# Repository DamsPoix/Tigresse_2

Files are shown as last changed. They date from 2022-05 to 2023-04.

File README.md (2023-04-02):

# Tigresse_2

<p align="center">
  
</p>

Ce projet nommé Tigresse-2 est un projet de Fusée expérimentale qui volera lors de la campagne de lancement 2022 organisé par le Centre National d'Etudes Spatiales. Cette campagne, nommée C'Space regroupe tous les clubs spatiaux de France et de temps en temps des clubs spatiaux d'autres pays. 
Tigresse-2 est la seconde fusée expérimentale de l'association de l'air et de l'espace de l'université d'Orléans Space Tech Orléans.

Elle emportera une expérience afin de mesurer les résonnances de Schumann durant sa phase de redescente sous parachute.

<p align="center">
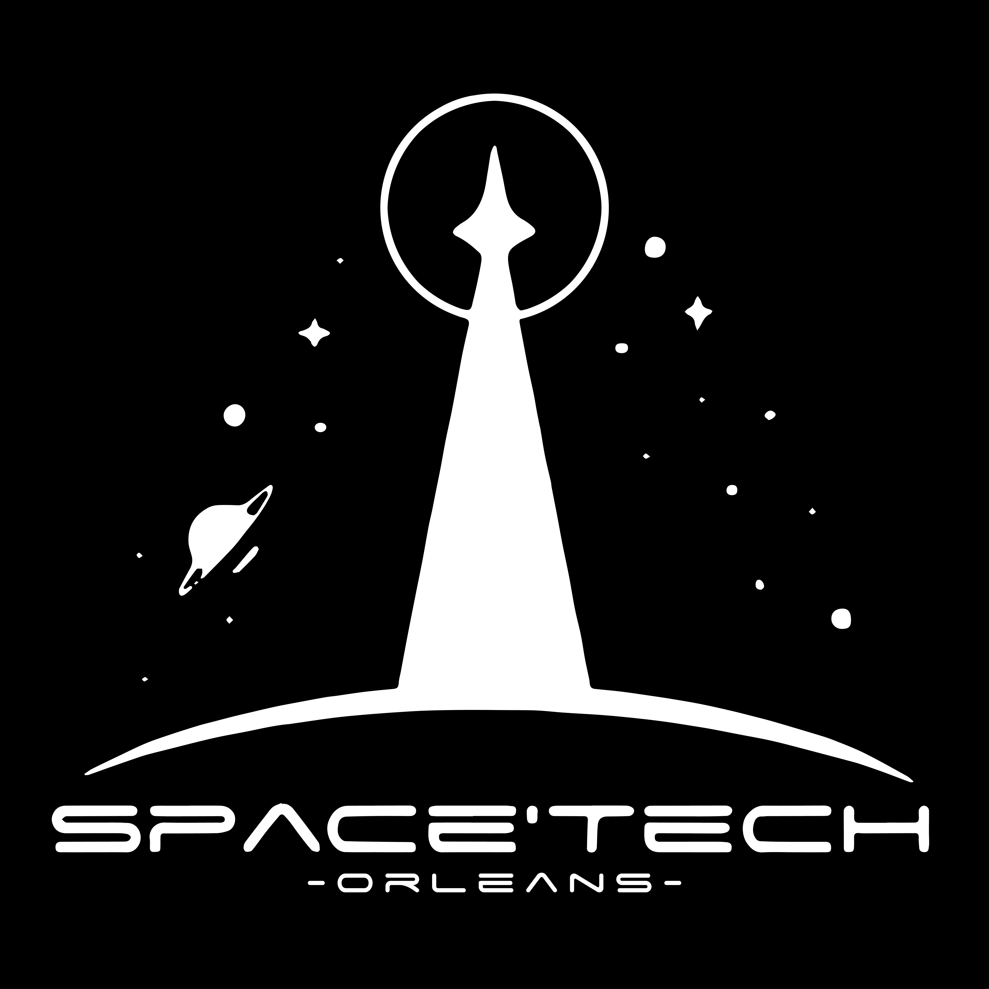
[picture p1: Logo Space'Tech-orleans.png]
  
</p>
La fusée a d'une hauteur de 1 mètre 85 avec une peau aluminium. L'ogive mesure 45cm.
<p align="center">
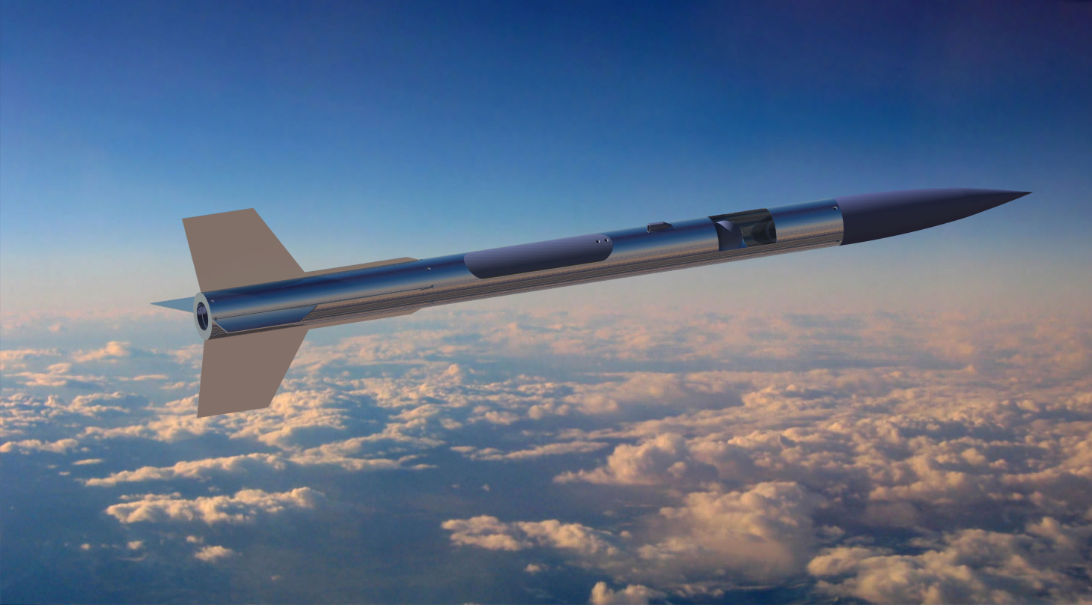
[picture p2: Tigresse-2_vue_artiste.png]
  
</p>
"""UPDATE"""

Après une campagne de lancements de fusées au C'Space 2022, Tigresse-2 a effectué un vol nominal ! 
Voici l'équipe qui a permit ce vol parfait : 

De gauche à droite : Aymerick BATS (responsable expérience) - Loup-Maël AGULES(support technique) - Raynald DUMAS (responsable vision fusée) - Léo MARMANDE (support technique) - Hugo KREMER (responsable mécanique) - Damien POIX (chef de projet/responsable seq et CAO) - Corentin LAROCHE (responsable télémétrie).
</p>
<p align="center">
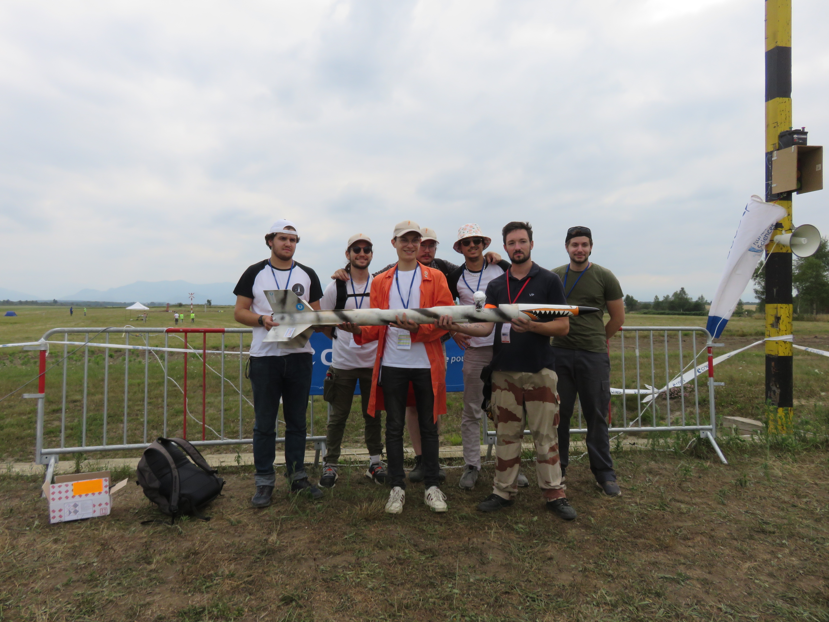
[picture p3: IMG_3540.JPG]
  
</p>

Lien vers GrabCad : <a href="https://grabcad.com/library/tigresse-2-1" target="_blank">Grabcad Tigresse-2</a>

Merci au CNES et à Planète Science pour cette opportunité ! 
Merci à l'équipe pour leur détermination et leur travail ! 

Go Space'Tech, Go Tigresse !

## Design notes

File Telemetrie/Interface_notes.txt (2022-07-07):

courbe avec la projection de trajectoire (+ data : altitude, acceleration, speed, timer)
carte avec la trajectoire vue de haut
attitude
stages (idle, liftoff, MECO, Apoapsis, Parachute deploy, landing)
logs (etats, erreurs, etat liaison GPS...)
control pannel :
	- enregistrer le raw data input (GQRX ou quoi, vraiment la Bande passante quoi)
	- exporter les données importante a sauvegarder au sol au cas ou (magnéto, GPS)
	- exporter la trajectoire pour récupération sur téléphone

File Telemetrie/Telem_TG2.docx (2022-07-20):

Télémétrie Tigresse

# Contexte

Dans le cadre du CSpace … t’as compris, la flemme. Avec un délais court de développement, de nombreux raccourcis ont été pris lors de la conception de ce système.

Cette documentation est clairement une ébauche.

# Besoins

La télémétrie doit permettre un suivi en temps réel et la récupération de la fusée après sa mission.

Elle sera constituée d’une charge utile et d’une station sol.

Un magnétomètre 3 axes devra être implémenté pour échantillonner les variations magnétiques pour l’expérience des résonnances de Schumann.

# Contraintes

Interdiction d’utiliser un récepteur télémétrique en zone pyrotechniques

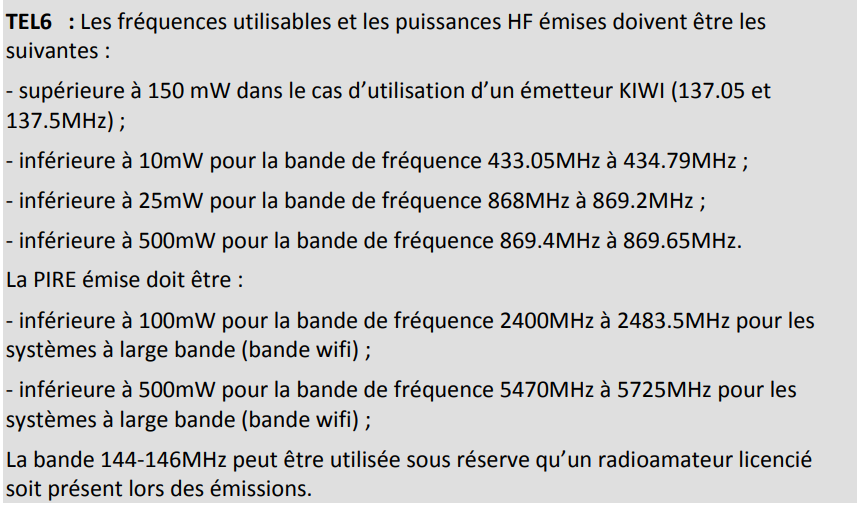
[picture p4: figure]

Alimentation indépendante, avec interrupteur de mise en marche indépendant.

Autonomie de 3h minimum.

Le Taux d’Onde Stationnaires (TOS) doit être inférieur à 2 pour la fréquence d’émission (avec connectique BNC).

Arrêtez l’émission 10 minutes après le lancement (Impératif)

# Problématiques

GPS : high rate / CoCom limit (< 18.000m & < 1000 knots)

Précision GPS

Perte de de signal GPS & Downlink

# Solutions proposées

## Charge utile :

La charge utile doit permettre l’envoie de donnée nécessaire au suivi et à la récupération de la fusée. Elle doit également permettre de valider et enregistrer les performances de celle-ci.

### Localisation :

Afin de permettre la localisation de la fusée dans l’espace, la CU devra embarquer un GPS, une centrale inertielle et un altimètre. Une fusion de ces 3 éléments doit permettre la localisation du lanceur à des fins de performances, et de tracking(si implémenté) par la station sol.

Le GPS sera de type 377-MAX-7Q-0

La centrale inertielle sera de type MPU9250 (toutes les IMU lowcost ont quasi les même specs dont autant pas se faire chier) et comprend le magnétomètre.

L’altimètre sera de type BMP390, pour une résolution ~25cm dans un cas ideal

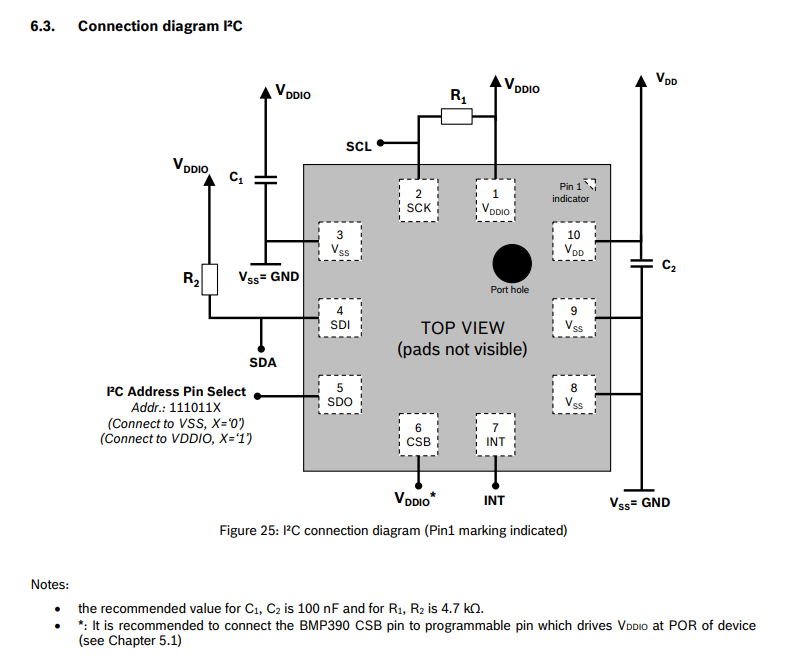
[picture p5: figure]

### Communication :

Une TTGO LoRa est souvent utilisé. Cependant, d’autres solution sont également disponible, comme l’utilisation d’un TX3H-869.5-10 avec un récepteur SDR. Un récepteur de type SDR impliquerait une plus grosse architecture (ordi et OS) au niveau de la station sol, mais reste envisageable a moindre coup.

Pour du 869MHz, le module TX3H-869 à une portée jusqu’à 3Km, et un débit de 10Kbps pour 450mW

Malgré la grosse consommation et le prix, ce module présente l’avantage d’une forte puissance d’émission.

On estime grâce a l’équation de friis que la perte est estimé à :

FreeSpaceLoss[dB]=32.5+20.log(2)+20.log(869)=97dB

On estime que pour une vitesse max de 250 m/s, l’effet doppler imposera une variation de fréquence de -724.583 Hz.

### Enregistrement :

Un stockage de masse devra permettre la journalisation des données. Il pourra s’agir d’une carte SD ou d’une EEPROM (comme sur la raspi pico). Etant donné le choix de l’OBC, il s’agira d’une carte SD.

### Processing :

L’OBC a déjà été choisi. Il est donc imposé, il s’agira d’une carte Adafruit Feather 32u4 Adalogger.

### Alimentation :

Module | Courant max | Tension d’alimentation
Adafruit Feather 32u4 Adalogger | 300mA | 3.3V
TX3H-869 | 350mA | 5V
BMP390 | 4µA | 3.3V
MPU9250 (shield) | 4mA | 5V
MAX-8Q-0 | 70mA | 3V

Comme la régulation se fait avec des régulateurs linéaires et pour une alimentation nominale de 7.4v, on trouve :

C=(0.3+0.35+0.004+0.07)=0.724 mAh

Pour 3h de fonctionnement, il faudrait donc une batterie de 2.17 mAh

Nous avons donc opté pour des batteries de type Li-ion car elles possèdent une capacité massique intéressante pour notre application.

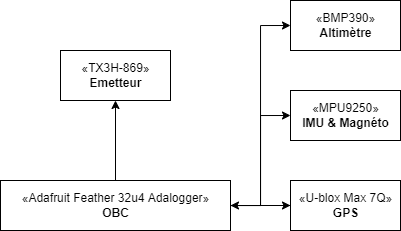
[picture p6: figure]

## Station sol :

La stations sol a plusieurs objectifs. Afficher les données brutes de l’état du lanceur, extrapoler la position du lanceur dans l’espace grâce à une fusion. Permettre de localiser et récupérer la fusée.

Il faudra également enregistrer les données reçues.

L’interface sera donc constituée de 3 sections :

- Données du lanceur (altitude, vitesse, stages, )
- Données de localisation par rapport à la station sol

Pour les données du lanceur, il faudra afficher :

- L’état de la liaison GPS
- L’état de la liaison télémétrique

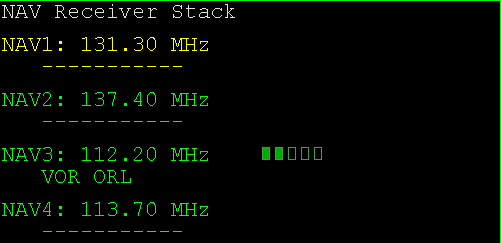
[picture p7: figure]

- L’altitude et vitesse actuelle

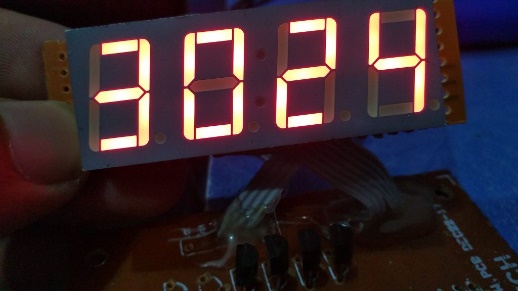
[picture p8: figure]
Arduino 4 digit 7 segment multiplexing on Atmega8 using ...

- Les étapes du lancement (Standby, Lift off, MECO, chute deployment, landing)

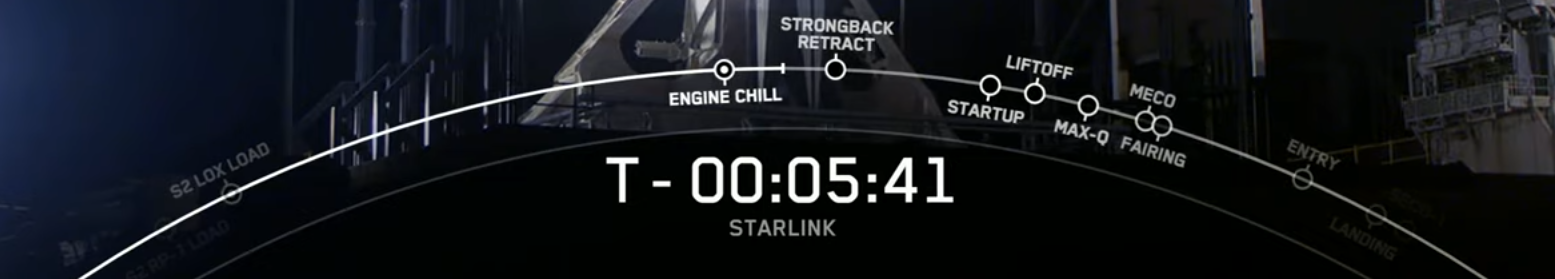
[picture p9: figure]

- La projection du vol

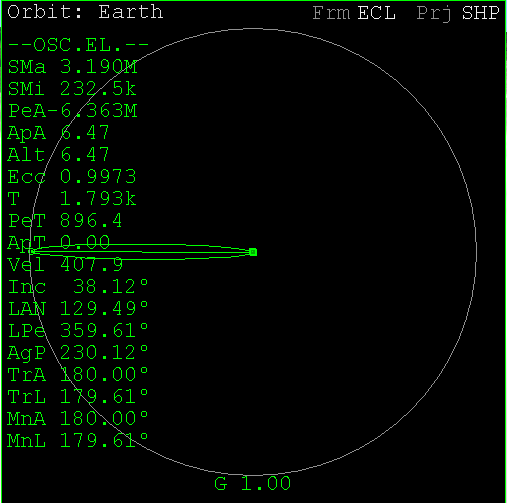
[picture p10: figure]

- Un journal de vol

Pour les données de récupération :

- La trajectoire du vol effectué sur une surface par rapport à notre position
- La distance et l’orientation par rapport à la position finale de la fusée

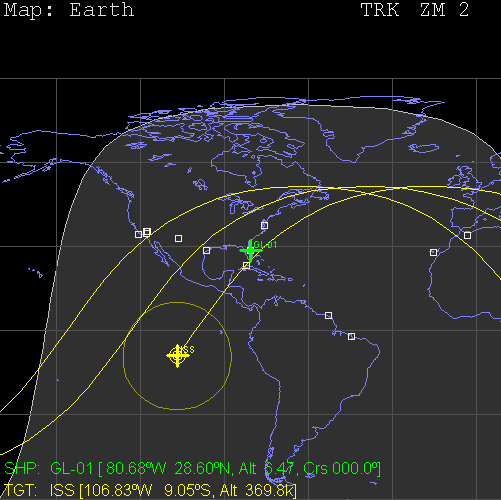
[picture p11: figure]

### Choix du hardware :

Pour la station sol, 2 solutions s’offres à nous. Dans le premier cas il s’agirait d’utiliser un ordinateur et un récepteur SDR :

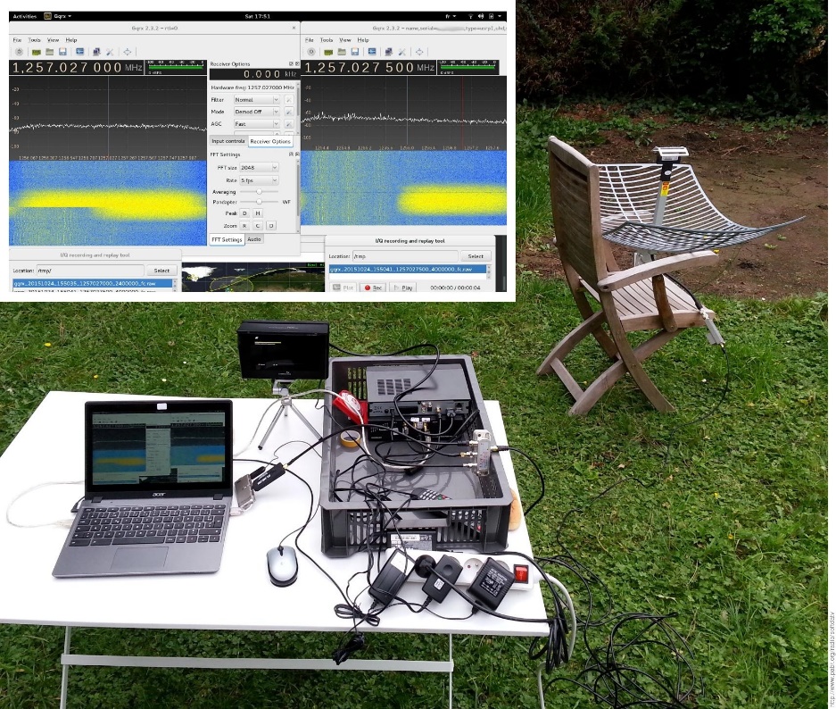
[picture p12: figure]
Receiving Digital Amateur TV from the ISS with an RTL-SDR

Ou d’utiliser une solution full hardware, ce qui rendrais l’installation plus fiable, mais plus complexe à développer :

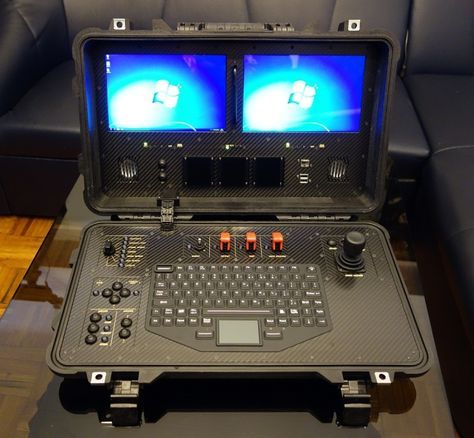
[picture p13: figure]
rugged UAV ground control station 1 | Uav, Diy drone ...

# Données transmises :

Les données qui transiteront entre la fusée et la station sol seront les suivantes :

- Altitude BMP
- Acceleration IMU
- Vertical speed (fusion IMU+BMP)
- Attitude (quaternion IMU)
- Raw GPS (permet la récupération de la fusée en cas de dérive de la fusion de données)
- Info stages et reception gps

# Design du nose cone :

Le type de design sera de type puissance. Le script python noConeGen.py permet de générer la courbe sous forme de dxf pour créer le cone.

# Carte télémétrie version 1 :

Après assemblage de la première version de la carte électronique sur PCB, quelques erreurs ont été relevé.

- Le montage mosfet du buzzer n’est pas correct. Une résistance a été temporairement branché en parallèle au buzzer afin de permettre à celui-ci de fonctionner correctement.
- Attention au sens de branchement de la puce GPS !!

# Calibration IMU

Pour la calibration IMU, utiliser le programme MPU9250CAL.ino et reporté les valeurs dans le programme principal.

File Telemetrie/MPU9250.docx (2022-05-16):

Mise en place du capteur MPU9250

La capteur MPU9250 est un capteur de suivi de mouvement 9 axes. Il est composé d’un gyroscope 3 axes, d’un accéléromètre 3 axes, d’un magnétomètre 3 axes, et d’un capteur de température. Le magnétomètre sera utilisé pour l’expérience sur les résonnances de Schumann. L’accéléromètre et le gyroscope sera utilisé pour la localisation de la fusée.

# Initialisation :

Dans un premier temps, il faudra développer une fonction d’initialisation du capteur pour les paramètres suivants :

Paramètre | Valeur
Communication | I2C
Gyroscope angular rate | +-500 °/s
Gyroscope low-pass filter | A déterminer
Gyroscope offsets (X, Y, Z) | A déterminer lors de la calibration
Accelerometer scale range | +-16g
Accelerometer offsets (X, Y, Z) | A déterminer lors de la calibration
Magnetometer offsets (X, Y, Z) | A déterminer lors de la calibration
Interruption | Sensor registers

# Acquisition :

Plusieurs solutions sont possibles pour l’acquisition des valeurs. On peut directement lire les données dans le Sensor Data Register qui contient les dernières valeurs des capteurs, ou alors utiliser la pile FIFO (First In First Out). Le registre FIFO doit être configuré auparavant. Cette méthode permet de récupérer les données par burst. Cependant, les données du magnétomètre ne peuvent pas être acquise via cette méthode. Le Sensor Data Register sera alors privilégié. Une interruption sera envoyée a chaque fois qu’une acquisition sera prête.

L’acquisition des capteurs ne doit commencer qu’après 100ms.

L’adresse I2C devrait être 0x68 ou 0x69 (0x = hexadécimal)

Il faudra donc récupérer les valeurs de l’accéléromètre, gyro, magnéto et capteur de température à chaque interruption. Et vérifier que les valeurs sont correctement calibrées.

# Traitement :

Un algorithme de fusion de données devra permettre de détermine la position de la fusée dans l’espace en fonction de l’angle et de l’intégration de l’accélération. Une fusion sera ensuite proposé avec le GPS et l’altimètre afin d’affiner les valeurs.

Références :

Datasheet : https://pdf1.alldatasheet.com/datasheet-pdf/view/1132035/TDK/MPU-9250.html

Arduino library : https://github.com/hideakitai/MPU9250

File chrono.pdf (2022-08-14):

Temps | Action | Lieu | Personne | Outil
| Installer batteries dans ogive et vérifier alimentation | Zone club | Corentin | Batteries
| Mettre piles dans module camera | Zone club | Raynald | Batteries 9V
| Dévisser la bague berry rocket et mettre les vis dans la boite vis | Tente club | Hugo | Clé allen 2.5 + boite vis
| Sortir bague berry rocket | Tente club | Hugo
| Dévisser attache trappe exp et mettre vis dans boite vis | Tente club | Hugo | Clé allen 2.5 + boite vis
| Dévisser bague boule exp et mettre vis dans boite vis | Tente club | Hugo | Clé allen 2.5 + boite vis
| décaller bague boule exp jusqu'à voir le logement batterie | Tente club | Hugo
| Insérer les batteries (8) | Tente club | Hugo | Batteries 6LF22
| Ré-enclancher bague boule exp | Tente club | Hugo
| Remettre en place bague berry rocket | Tente club | Hugo
| Visser bague berry rocket | Tente club | Hugo | 1 vis M4
| Mettre attache trappe exp | Tente club | Hugo | Attache trappe exp
| Dévisser vis bague arrière parachute | Tente club | Raynald | Clé allen 2.5
| Dévisser patin et mettre les vis dans la boite vis | Tente club | Hugo, Raynald | Clé allen 2.5
| Décaller bague parachute au maximum | Tente club | Hugo, Raynald
| Vérifier position intérupteur caméra | Tente club | Hugo, Raynald | Module camera
| Brancher cosse 3,7V | Tente club | Raynald
| Brancher cosse 9V | Tente club | Raynald
| Brancher caméra 1 et 2, vérifier led verte et bleu | Tente club | Raynald
| Switch ON/OFF, vérifier l'allumage de la led blanche | Tente club | Raynald
| Appuyer bouton caméra 1 et 2 et vérifier que les leds sur les cameras ne clignottent plus | Tente club | Raynald
| Insertion du module camera dans la fusée | Tente club | Hugo, Raynald
| Vissage du module caméra sur la peau de la fusée | Tente club | Hugo, Raynald | Clé allen 2 + 4 vis M3
| Remettre en position la bague parachute | Tente club | Hugo, Raynald
| Visser bague parachute | Tente club | Hugo, Raynald | Clé allen 2.5 + 1 vis M4
| Visser patin | Tente club | Hugo, Raynald | Clé allen 2.5 + 1 vis M4
| Visser boucle parachute et serrer les écrous | Tente club | Hugo | Clé plate 13 + écrou M10
| Etendre parachute et plier en accordéon | Tente club | Hugo | Parachute
| Remise en place du parachute dans la case | Tente club | Hugo | Parachute
| Brancher une pile 9V parachute | Tente club | Hugo, Raynald | Pile 9V
| Appuyer sur bouton parachute pour refermer la trappe | Tente club | Hugo, Raynald
| Débrancher pile 9V et remettre dans le batterie bag | Tente club | Hugo | Pile 9V
| Mettre en place et visser la bague berry rocket | Tente club | Aymerick | Clé allen 2.5 + 1 vis M4
| Poser la fusée sur les supports fusée | Pas de tir | Hugo | Supports fusée (2)
| Mettre le mode test | Pas de tir
| Insérer Jack | Pas de tir | Aymerick | Câble jack
Déplacer bague batteries et brancher les piles 9V précédemment insérées dans le logement | Pas de tir | Hugo
Vérifier led supply et jack | Pas de tir
Enclancher bague boule exp | Pas de tir | Hugo
Visser bague boule expérience | Pas de tir | Hugo | Clé allen 2.5 + vis M4
Visser support trappe exp | Pas de tir | Hugo | Support trappe exp + Clé allen 2.5 + 2 vis M4
Installer trappe exp en appuyant sur le bouton trappe exp et en ajoutant mousse | Pas de tir | Hugo | Mousse
Demander autorisation télém | Pas de tir | Corentin
Allumer télém après autorisation | Pas de tir | Corentin
Vérification télém sur ordinateur Corentin + bip d'initialisation | Pas de tir | Corentin | Ordinateur + SDR
Visser ogive sur fusée | Pas de tir | Corentin | Clé allen 2.5 + 4 vis M4
Passer en mode vol | Pas de tir | Aymerick
Vérifier mode vol | Pas de tir | Hugo
Insérer fusée dans rampe | Pas de tir | Hugo, Corentin
Accrocher Jack sur rampe | Pas de tir | Aymerick

pack batteries
Ordinateur coco+sdr

Outil à emmener
Kit clé allen
Kit tourne vis
Boite à pince
Cameras
support fusée

scotch

mousse

pack vis

boite à vis

fusée

câble jack

Clé plate

### 2 rondelles

### 4 écrous

bridage

Parachute

télem

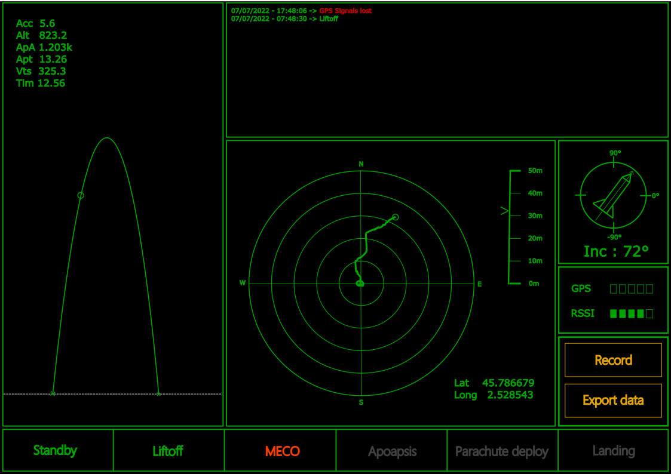
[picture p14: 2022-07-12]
Telemetrie/designInterface.png

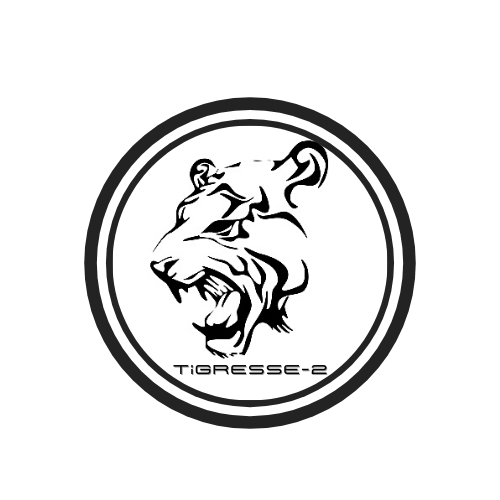
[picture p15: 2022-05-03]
Tigresse-2.png

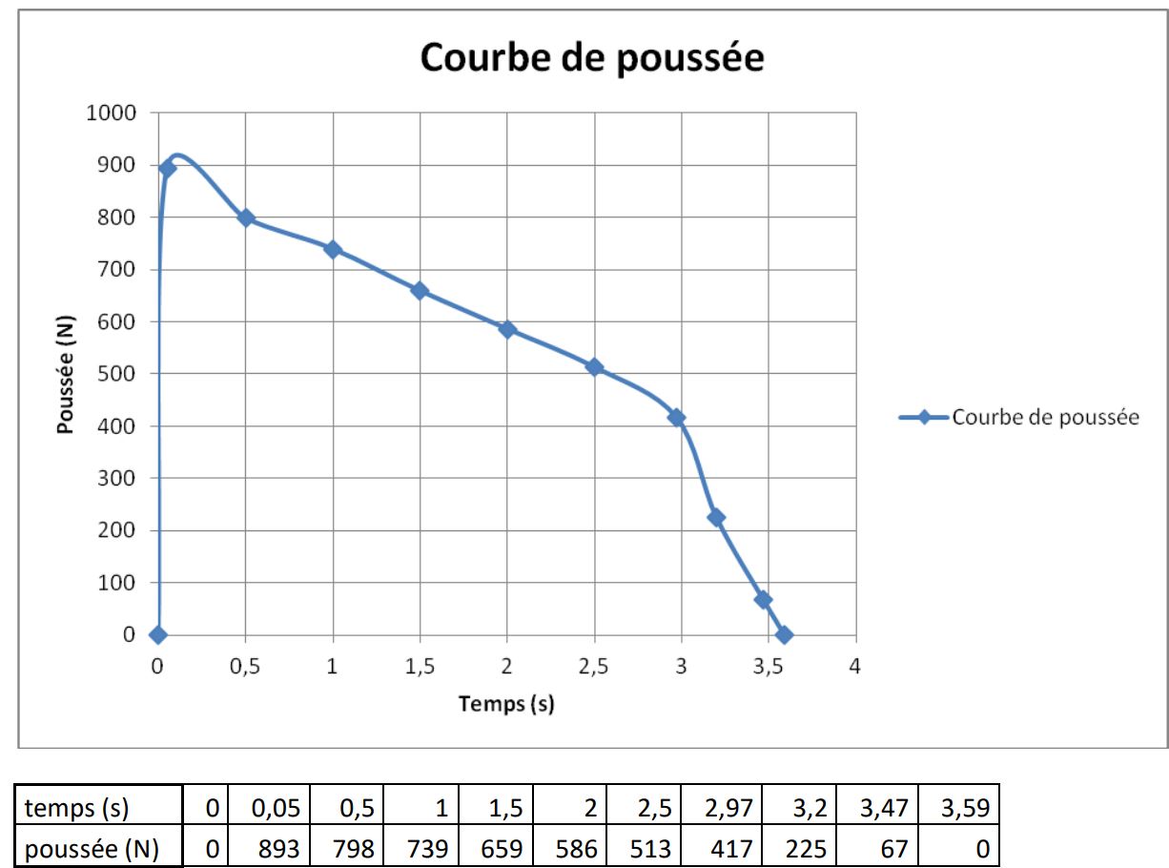
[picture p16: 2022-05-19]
Moteur/caractéristiques_moteur.JPG

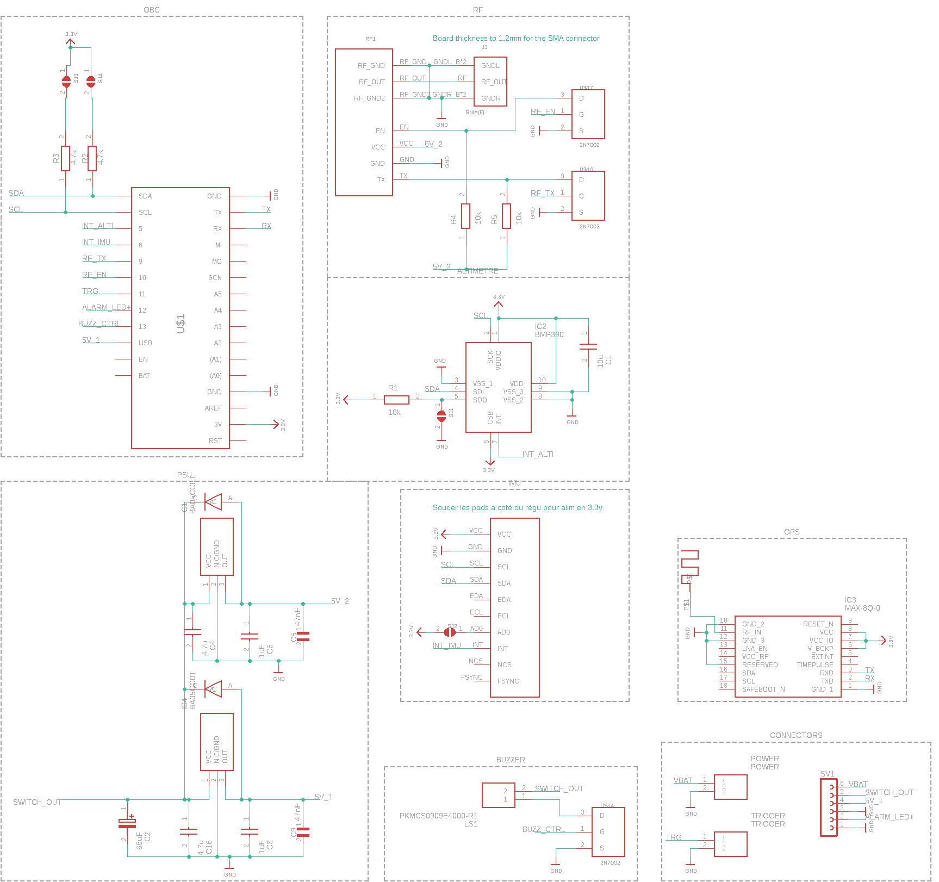
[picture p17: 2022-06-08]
Telemetrie/Telem_TG2_schema.png

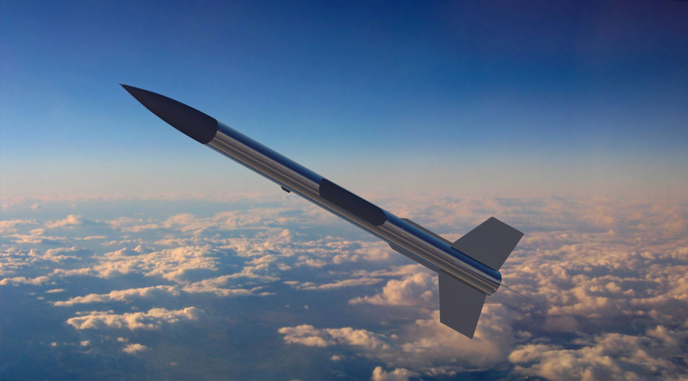
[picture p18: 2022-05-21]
Modélisation_3D/Rendu_Github.jpg

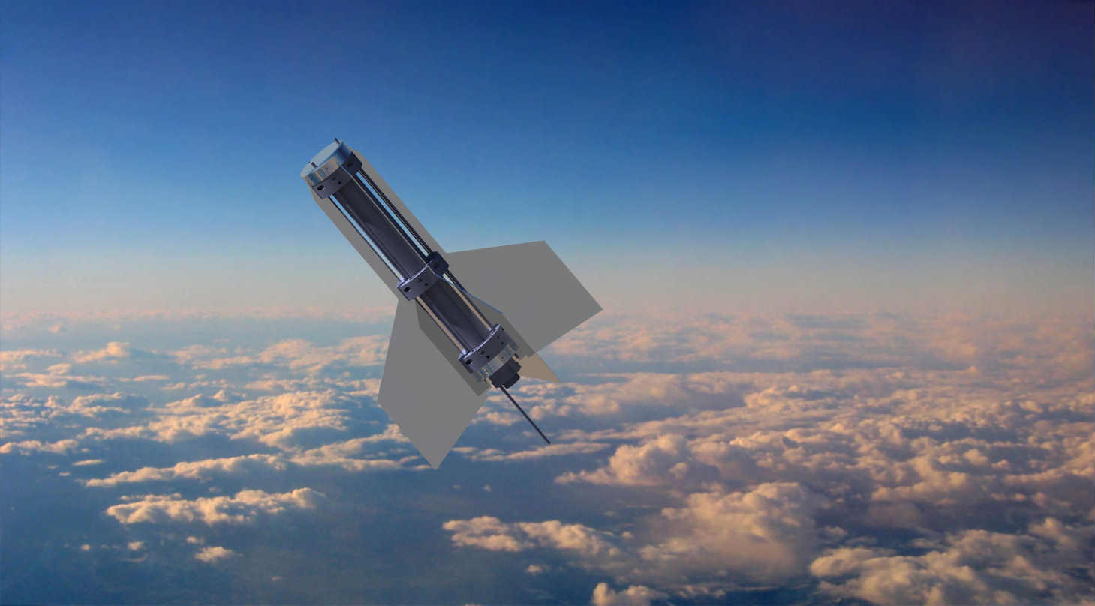
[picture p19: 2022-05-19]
Modélisation_3D/Rendu poussée.jpg

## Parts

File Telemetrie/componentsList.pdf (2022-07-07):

Liste Composants telem

Ref | Prix | Quantité | total | Achat | Datasheet | commandé | reçu
Feather M0 adalogger | 21,95 | 1 | 21,95 https://www.adafruit.com/product/2796 https://learn.adafruit.com/adafruit-feather-m0-adalogger/downloads
TX3H-869 | 38,04 | 1 | 38,04 https://www.lextronic.fr/emetteur-tx3h-869-625.html http://www.radiometrix.com/files/additional/tx3h.pdf
BMP390 | 4,83 | 1 | 4,83 https://www.mouser.fr/ProductDetail/Bosch-Sensortec/BMP390?qs=QNEnbhJQKvYQVfvRMgo2YA%3D%3D https://www.mouser.fr/datasheet/2/783/bst_bmp390_ds002-2448819.pdf
MPU9250 | 15,38 | 1 | 15,38 https://www.amazon.fr/gp/product/B075XSBT3Y/ref=ppx_yo_dt_b_asin_title_o00_s00?ie=UTF8&psc=1 https://pdf1.alldatasheet.com/datasheet-pdf/view/1132035/TDK/MPU-9250.html
Bat connector | 0,44 | 2 | 0,88 https://www.mouser.fr/ProductDetail/Molex/90156-0142?qs=jBHU5RPckUotmv8DXiRxUw%3D%3D https://www.mouser.fr/datasheet/2/276/1/0901560142_CRIMP_HOUSINGS-176781.pdf
board connector | 1,29 | 2 | 2,58 https://www.mouser.fr/ProductDetail/Molex/90136-1202?qs=zF2Np9wwC%252B7fqKXQTHeKiQ%3D%3D https://www.mouser.fr/datasheet/2/276/3/0901361202_PCB_HEADERS-2834796.pdf
Ublox Max 8Q | 21,45 | 1 | 21,45 https://www.mouser.fr/ProductDetail/u-blox/MAX-8Q-0?qs=DPoM0jnrROXs29tEjk5Xmw%3D%3D https://www.mouser.fr/datasheet/2/1025/MAX_8_DataSheet__UBX_16000093_-1915290.pdf
18650- | 25,57 | 1 | 25,57 https://fr.rs-online.com/web/p/blocs-batteries-rechargeables/1449410 https://docs.rs-online.com/c215/0900766b8163e9cb.pdf
10k res - 0603 | ERJ-UP3D1002V | 0,304 | 3 | 0,912 https://www.mouser.fr/ProductDetail/Panasonic/ERJ-UP3D1002V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 https://www.mouser.fr/datasheet/2/315/Panasonic_Resistors_Thick_Film_Anti_Sulf_Anti_Surg-1825099.pdf
10µF Ceramic capa 0805 6,3V | CGA4J1X7R0J106K125AC | 0,39 | 1 | 0,39 https://www.mouser.fr/ProductDetail/TDK/CGA4J1X7R0J106K125AC?qs=NRhsANhppD%2FK4ZRLurir6Q%3D%3D https://product.tdk.com/system/files/dam/doc/product/capacitor/ceramic/mlcc/catalog/mlcc_automotive_general_en.pdf
4,7k res - 0603 | ERJ-UP3D4701V | 0,35 | 2 | 0,7 https://www.mouser.fr/ProductDetail/Panasonic/ERJ-UP3D4701V?qs=GedFDFLaBXFb98Nz2Hqatg%3D%3D https://www.mouser.fr/datasheet/2/315/Panasonic_Resistors_Thick_Film_Anti_Sulf_Anti_Surg-1825099.pdf
Antenne | 7,69 | 1 | 7,69 https://www.mouser.fr/ProductDetail/?qs=P1JMDcb91o7IOmGnFabR3w%3D%3D https://www.mouser.fr/datasheet/2/398/TI.85.2113-1623698.pdf
MOSFET | 2N7002L | 0,27 | 3 | 0,81 https://www.mouser.fr/ProductDetail/onsemi-Fairchild/2N7002L?qs=C8E66ftkQtwY2xWJIiLLvA%3D%3D https://www.mouser.fr/datasheet/2/308/1/2N7002L_FCS_D-2934378.pdf
SMA | 5,14 | 1 | 5,14 https://www.mouser.fr/ProductDetail/Linx-Technologies/CONSMA020.042-G?qs=7D1LtPJG0i3DlJhqoQK7wQ%3D%3D https://linxtechnologies.com/wp/wp-content/uploads/consma020.042-g-ds.pdf
Capa chimique 68 µF | EEE-FT1C680AR | 1,77 | 1 | 1,77 https://fr.rs-online.com/web/p/condensateurs-electrolytiques/9213270 https://docs.rs-online.com/b54e/0900766b814b8faf.pdf
buzzer | PKMCS0909E4000-R1 | 1,123 | 1 | 1,123 https://fr.rs-online.com/web/p/buzzers-piezo/9010898 https://docs.rs-online.com/d315/0900766b81465df1.pdf
regu ldo 5v | BA05CC0T | 2,17 | 2 | 4,34 https://www.mouser.fr/ProductDetail/ROHM-Semiconductor/BA05CC0T?qs=4kLU8WoGk0t9NPk8txP65Q%3D%3D https://www.mouser.fr/datasheet/2/348/baxxdd0-e-1873983.pdf
capa ceram 4,7uF | C2012X5R1H475K125AB | 0,187 | 2 | 0,374 https://fr.rs-online.com/web/p/condensateurs-ceramique-multicouches/1084050 https://docs.rs-online.com/b939/0900766b81714c17.pdf
diode | VS-30BQ100-M3/9AT | 0,586 | 2 | 1,172 https://fr.rs-online.com/web/p/diodes-schottky-et-de-redressements/1652283 https://docs.rs-online.com/89b9/0900766b80791051.pdf
capa ceram 1uF | CGA8P3X7T2E105K250KA | 1,757 | 2 | 3,514 https://fr.rs-online.com/web/p/condensateurs-ceramique-multicouches/9155477 https://docs.rs-online.com/659c/0900766b814e90e4.pdf
capa ceram 47nF | 06035C473K4T2A | 0,08 | 2 | 0,16 https://fr.farnell.com/avx/06035c473k4t2a/cond-0-047-f-50v-10-x7r-0603/dp/2566061 https://www.farnell.com/datasheets/2918449.pdf
Total | 158,775

Liste Composants telem

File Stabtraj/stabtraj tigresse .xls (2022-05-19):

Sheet: Trajecto
 |  | TRAJECTO
 |  | Trajectographie de fusée
 |  | Remplir les cases jaunes
 |  | Fusée
 | Nom | 0
 | Club | Mon club
 | Masse totale | 7.734 kg
 | Propulseur | Barasinga (Pro54-5G)
 |  | Traînée Aérdynamique
 | Surface Réf. | 0.009134 m²
 | Cx | 0.6
 |  | Rampe de Lancement
 | Longueur | 4 m
 | Élévation | 85 °
 | Altitude | 0 m
 |  | DescenteSousParachute |  |  |  | 2021-06-06 | Temps | Altitude z | Portée x | Vitesse | Accélération | Efforts
 |  | Fusée | 0 satellite |  | Sortie de Rampe |  |  |  |  | 28.2 m/s
 | Masse | 6.701 kg | 1 kg |  | Vit max & Acc max |  |  |  |  | 216.1719542 m/s | 105.786819 m/s²
 | Dépotage | N/A |  |  | Largage du satellite |  | 3.5 s | 477.4614643 m | 51.15783747 m | 212.7291735 m/s |  | 2771.8 N
 | Ouverture para | 17 s | 3.5 s |  | Culmination, Apogée |  | 17.8 s | 1699.035094 m | 288.6509889 m | 13.72343158 m/s
 | Surface para | 1.05 m² | 0.1 m² |  | Ouverture parachute fusée |  | 17.0 s | 1695.509044 m | 277.6522132 m | 16.11450197 m/s |  | 167.0 N
 | Cx parachute | 1 | 1 |  | Impact balistique |  | 39.0 s |  | 512.68624 m | 128.7 m/s |  | 55480.28788 J
 | Vitesse du vent | 5 m/s | 5 m/s
 | Vitesse descente | 10.1 m/s | 12.7 m/s
 | Durée descente | 167.7040281 s | 37.72739929 s |  |  |  | Pour localiser la fusée
 | Durée du vol | 184.7040281 s | 41.22739929 s |  | Couleur fuselage/coiffe |  | Brun/Orange…
 | Déport latéral | ±838.5201404 m | ±188.6369965 m |  | Couleur parachute fusée |  | Rouge |  |  |  |  |  | fichier initial
 |  |  |  |  | Couleur parachute satellite |  | Jaune |  |  |  |  |  | propu OK
 | Commentaire libre : |  |  |  |  |  |  |  |  |  |  |  | v3.3
Calcul de la surface d'un parachute |  |  |  |  | Résultats détaillés |  | Temps | Altitude z | Portée x | Vitesse | Accélération | Angle
 |  |  |  |  |  |  | s | m | m | m/s | m/s² | °
 |  |  |  |  | Décollage |  | 0 | 0 | 0 | 0 | - | 85
 |  |  |  |  | Sortie de Rampe |  | 0.30 | 3.87 | 0.34 | 28.2 | 100.4 | 85.0
 | Longeur du bord |  |  |  | Vit max & Acc max |  | - | - | - | 216.1719542 | 105.8 | -
 | 459 mm |  |  |  | Fin de Propulsion |  | 3.6 | 498.4636589 | 53.57207818 | 209.9569299 | 30.8 | 83.4
 | Largeur du coté |  |  |  | Culmination, Apogée |  | 17.8 | 1699.035094 | 288.6509889 | 13.72343158 | 9.8 | 2.0
 | 459 mm |  |  |  | Impact balistique |  | 39.0 | ~0 | 512.68624 | 128.681034 | 1.6 | -87.3
 | Surface para |  |  |  | Ouverture parachute fusée |  | 17.0 | 1695.509044 | 277.6522132 | 16.11450197 | 9.9 | 31.2
 | 1.05 m² |  |  |  | Impact fusée sous para. |  | 184.7040281 | ~0 | -561 | 1116 | 10.11012713 | 9.8 | -
 |  |  |  |  | Largage du satellite |  | 3.5 | 477.4614643 | 51.15783747 | 212.7291735 | 23.5 | 83.5
 |  |  |  |  | Impact du satellite |  | 41.22739929 | ~0 | -137 | 240 | 12.65556262 | 9.8 | -
 | Rayon
 | 600 mm
 | Surface para
 | 1.13 m²
 | Vitesse de descente sous parachute :
 | Textes pour les listes déroulantes et graphiques :
 | 0 satellite |  |  |  | N/A | Délais dépotage
 | 1 satellite |  |  |  | -9.0 s | -9
 | Phase ascendante |  |  |  | -7.0 s | -7
 | Descente balistique |  |  |  | -5.0 s | -5
 | Fusée sous parachute |  |  |  | -3.0 s | -3
 |  |  |  |  | 0.0 s | -0
 | Trajectoire (x z) |  |  |  | autre
 | Portée x [m]
 | Temps [s]
 | Altitude z / Temps
 | T_para = | 17
 | Données pour les graphiques :
 | xz max | xz max
 | 1699.035094 | 1699.035094
 | x para | z para
 | 277.6522132 | 1695.509044
 | 277.6522132 | 847.7545219
 | 277.6522132 | 0
 | 320.0399393 | 84.77545219
 | 277.6522132 | 0
 | 235.2644871 | 84.77545219
 | 277.6522132 | 0
 | t para | z para
 | 17.0 | 1695.509044 |  | 1 | vertical
 | 100.9 | 847.7545219 |  | 1 | horizontal
 | 184.7 | 0 |  |  | flèches
 | 183.1 | 52.16138938 |  | 1s | 3.90
 | 184.7 | 0 |  | t/T | 0.91
 | 179.2 | 19.58839255 |  | z/Z | 1.00
 | 184.7 | 0
 | x sat | z sat
 | FALSE | FALSE
 | FALSE | FALSE
 | FALSE | FALSE
 | FALSE | FALSE
 | FALSE | FALSE
 | FALSE | FALSE
 | FALSE | FALSE
 | t sat | z sat
 | FALSE | FALSE
 | 0.0 | 0
 | FALSE | FALSE
 | FALSE | FALSE
 | FALSE | FALSE |  | t/T | 0.91
 | FALSE | FALSE |  | z/Z | 0.94
 | FALSE | FALSE
 | t | z | x
 | 4.25 | 847.7545219 | 69.4130533
 | 28.4 | 849.5175472 | 438.007823
 | z_triomphe | x_triomphe | Arc de triomphe |  | Arc de triomphe
 | #N/A | 0 | 288.6509889 |  | 288.6509889
 | #N/A | 23 | 311.6509889 |  | 265.6509889
 | #N/A | 23 | 311.6509889 |  | 265.6509889
 | #N/A | 0 | 288.6509889 |  | 288.6509889
 | #N/A | 23 | 311.6509889 |  | 265.6509889
 | #N/A | 23 | 311.6509889 |  | 265.6509889
 | #N/A | 8 | 296.6509889 |  | 280.6509889
 | #N/A | 8 | 296.6509889 |  | 280.6509889
 | #N/A | 23 | 311.6509889 |  | 265.6509889
 | #N/A | 8 | 296.6509889 |  | 280.6509889
 | #N/A | 7.6 | 296.2509889 |  | 281.0509889
 | #N/A | 6.8 | 295.4509889 |  | 281.8509889
 | #N/A | 6 | 294.6509889 |  | 282.6509889
 | #N/A | 5 | 293.6509889 |  | 283.6509889
 | #N/A | 3.8 | 292.4509889 |  | 284.8509889
 | #N/A | 0 | 288.6509889 |  | 288.6509889
 | z_Eiffel | x_Eiffel | Tour Eiffel |  | Tour Eiffel
 | 324 | 0 | 288.6509889 |  | 288.6509889
 | 300 | 0 | 288.6509889 |  | 288.6509889
 | 280 | 10 | 298.6509889 |  | 278.6509889
 | 280 | 0 | 288.6509889 |  | 288.6509889
 | 280 | 10 | 298.6509889 |  | 278.6509889
 | 200 | 13 | 301.6509889 |  | 275.6509889
 | 160 | 17 | 305.6509889 |  | 271.6509889
 | 115 | 20 | 308.6509889 |  | 268.6509889
 | 90 | 25 | 313.6509889 |  | 263.6509889
 | 57 | 30 | 318.6509889 |  | 258.6509889
 | 40 | 36 | 324.6509889 |  | 252.6509889
 | 20 | 48 | 336.6509889 |  | 240.6509889
 | 0.5 | 62 | 350.6509889 |  | 226.6509889
 | 0.5 | 37 | 325.6509889 |  | 251.6509889
 | 15 | 30 | 318.6509889 |  | 258.6509889
 | 30 | 15 | 303.6509889 |  | 273.6509889
 | 37 | 0 | 288.6509889 |  | 288.6509889
 | 67 | 0 | 288.6509889 |  | 288.6509889
 | 67 | 17 | 305.6509889 |  | 271.6509889
 | 100 | 11 | 299.6509889 |  | 277.6509889
 | 100 | 0 | 288.6509889 |  | 288.6509889

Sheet: Propu
Moteur sélectionné | Ligne
Barasinga (Pro54-5G) | 254 | I_total | 2058.4 N.s | ISP | 203.1206673 s | MpropuPlein | 1.685 kg | m_poudre | 1.033 kg | MpropuVide | 0.652 kg | XpropuPlein | 250 mm | XpropuVide | 240 mm | Longueur | 488 mm | Diamètre | 54 mm | Type | Fusex | Combustion | 0.0 s | Dépotage | 0
Temps (en s) | 0 | 0.05 | 0.5 | 1 | 1.5 | 2 | 2.5 | 2.97 | 3.2 | 3.47 | 3.59 | 3.59 | 3.59 | 3.59 | 3.59 | 3.59 | 3.59 | 3.59 | 3.59 | 3.59 | 3.59 | 3.59 | 3.59 | 1000
Poussée (en N) | 0 | 893 | 798 | 739 | 659 | 586 | 513 | 417 | 225 | 67 | 0 | 0 | 0 | 0 | 0 | 0 | 0 | 0 | 0 | 0 | 0 | 0 | 0 | 0
H2O
H2O 1.5L 300g 6bar | 26 | I_total | 9.8 N.s | ISP | 3.3 s | MpropuPlein | 0.3 kg | M_éjecté | 0.3 kg | M_burnout | 0 kg | XpropuPlein | 60 mm | XpropuVide | 150 mm | Longueur | 300 mm | Diamètre | 90 mm | Type | H2O
Temps (en s) | 0 | 0.001 | 0.02 | 0.038 | 0.04 | 0.04 | 0.04 | 0.04 | 0.04 | 0.04 | 0.04 | 0.04 | 0.04 | 0.04 | 0.04 | 0.04 | 0.04 | 0.04 | 0.04 | 0.04 | 0.04 | 0.04 | 0.04 | 1000
Poussée (en N) | 0 | 310 | 250 | 212 | 0 | 0 | 0 | 0 | 0 | 0 | 0 | 0 | 0 | 0 | 0 | 0 | 0 | 0 | 0 | 0 | 0 | 0 | 0 | 0
I_total_i (en N.s) | 0.2 | 5.3 | 4.2 | 0.2 | 0 | 0 | 0 | 0 | 0 | 0 | 0 | 0 | 0 | 0 | 0 | 0 | 0 | 0 | 0 | 0 | 0 | 0 | 0
H2O 1.5L 450g 6bar | 31 | I_total | 13.8 N.s | ISP | 3.1 s | MpropuPlein | 0.45 kg | M_éjecté | 0.45 kg | M_burnout | 0 kg | XpropuPlein | 90 mm | XpropuVide | 150 mm | Longueur | 300 mm | Diamètre | 90 mm | Type | H2O
Temps (en s) | 0 | 0.001 | 0.02 | 0.04 | 0.061 | 0.062 | 0.062 | 0.062 | 0.062 | 0.062 | 0.062 | 0.062 | 0.062 | 0.062 | 0.062 | 0.062 | 0.062 | 0.062 | 0.062 | 0.062 | 0.062 | 0.062 | 0.062 | 1000
Poussée (en N) | 0 | 310 | 245 | 200 | 167 | 0 | 0 | 0 | 0 | 0 | 0 | 0 | 0 | 0 | 0 | 0 | 0 | 0 | 0 | 0 | 0 | 0 | 0 | 0
I_total_i (en N.s) | 0.2 | 5.3 | 4.5 | 3.9 | 0.1 | 0 | 0 | 0 | 0 | 0 | 0 | 0 | 0 | 0 | 0 | 0 | 0 | 0 | 0 | 0 | 0 | 0 | 0
H2O 1.5L 600g 6bar | 36 | I_total | 17.1 N.s | ISP | 2.9 s | MpropuPlein | 0.6 kg | M_éjecté | 0.6 kg | M_burnout | 0 kg | XpropuPlein | 120 mm | XpropuVide | 150 mm | Longueur | 300 mm | Diamètre | 90 mm | Type | H2O
Temps (en s) | 0 | 0.001 | 0.02 | 0.04 | 0.06 | 0.08 | 0.088 | 0.089 | 0.089 | 0.089 | 0.089 | 0.089 | 0.089 | 0.089 | 0.089 | 0.089 | 0.089 | 0.089 | 0.089 | 0.089 | 0.089 | 0.089 | 0.089 | 1000
Poussée (en N) | 0 | 310 | 240 | 190 | 157 | 133 | 125 | 0 | 0 | 0 | 0 | 0 | 0 | 0 | 0 | 0 | 0 | 0 | 0 | 0 | 0 | 0 | 0 | 0
I_total_i (en N.s) | 0.2 | 5.2 | 4.3 | 3.5 | 2.9 | 1 | 0.1 | 0 | 0 | 0 | 0 | 0 | 0 | 0 | 0 | 0 | 0 | 0 | 0 | 0 | 0 | 0 | 0
H2O 1.5L 750g 6bar | 41 | I_total | 19.4 N.s | ISP | 2.6 s | MpropuPlein | 0.75 kg | M_éjecté | 0.75 kg | M_burnout | 0 kg | XpropuPlein | 150 mm | XpropuVide | 150 mm | Longueur | 300 mm | Diamètre | 90 mm | Type | H2O
Temps (en s) | 0 | 0.001 | 0.02 | 0.04 | 0.06 | 0.08 | 0.1 | 0.123 | 0.124 | 0.124 | 0.124 | 0.124 | 0.124 | 0.124 | 0.124 | 0.124 | 0.124 | 0.124 | 0.124 | 0.124 | 0.124 | 0.124 | 0.124 | 1000
Poussée (en N) | 0 | 310 | 230 | 175 | 140 | 118 | 100 | 85 | 0 | 0 | 0 | 0 | 0 | 0 | 0 | 0 | 0 | 0 | 0 | 0 | 0 | 0 | 0 | 0
I_total_i (en N.s) | 0.2 | 5.1 | 4 | 3.1 | 2.6 | 2.2 | 2.1 | 0.0425 | 0 | 0 | 0 | 0 | 0 | 0 | 0 | 0 | 0 | 0 | 0 | 0 | 0 | 0 | 0
H2O 2.0L 400g 6bar | 46 | I_total | 12.9 N.s | ISP | 3.3 s | MpropuPlein | 0.5 kg | M_éjecté | 0.4 kg | M_burnout | 0.1 kg | XpropuPlein | 60 mm | XpropuVide | 150 mm | Longueur | 300 mm | Diamètre | 98 mm | Type | H2O
Temps (en s) | 0 | 0.001 | 0.02 | 0.04 | 0.05 | 0.051 | 0.051 | 0.051 | 0.051 | 0.051 | 0.051 | 0.051 | 0.051 | 0.051 | 0.051 | 0.051 | 0.051 | 0.051 | 0.051 | 0.051 | 0.051 | 0.051 | 0.051 | 1000
Poussée (en N) | 0 | 310 | 264 | 230 | 213 | 0 | 0 | 0 | 0 | 0 | 0 | 0 | 0 | 0 | 0 | 0 | 0 | 0 | 0 | 0 | 0 | 0 | 0 | 0
I_total_i (en N.s) | 0.2 | 5.5 | 4.9 | 2.2 | 0.1 | 0 | 0 | 0 | 0 | 0 | 0 | 0 | 0 | 0 | 0 | 0 | 0 | 0 | 0 | 0 | 0 | 0 | 0
H2O 2.0L 600g 6bar | 51 | I_total | 18.1 N.s | ISP | 3.1 s | MpropuPlein | 0.7 kg | M_éjecté | 0.6 kg | M_burnout | 0.1 kg | XpropuPlein | 90 mm | XpropuVide | 150 mm | Longueur | 300 mm | Diamètre | 98 mm | Type | H2O
Temps (en s) | 0 | 0.001 | 0.02 | 0.04 | 0.06 | 0.08 | 0.081 | 0.081 | 0.081 | 0.081 | 0.081 | 0.081 | 0.081 | 0.081 | 0.081 | 0.081 | 0.081 | 0.081 | 0.081 | 0.081 | 0.081 | 0.081 | 0.081 | 1000
Poussée (en N) | 0 | 310 | 260 | 220 | 190 | 167 | 0 | 0 | 0 | 0 | 0 | 0 | 0 | 0 | 0 | 0 | 0 | 0 | 0 | 0 | 0 | 0 | 0 | 0
I_total_i (en N.s) | 0.2 | 5.4 | 4.8 | 4.1 | 3.6 | 0.1 | 0 | 0 | 0 | 0 | 0 | 0 | 0 | 0 | 0 | 0 | 0 | 0 | 0 | 0 | 0 | 0 | 0
H2O 2.0L 800g 6bar | 56 | I_total | 22.6 N.s | ISP | 2.9 s | MpropuPlein | 0.9 kg | M_éjecté | 0.8 kg | M_burnout | 0.1 kg | XpropuPlein | 120 mm | XpropuVide | 150 mm | Longueur | 300 mm | Diamètre | 98 mm | Type | H2O
Temps (en s) | 0 | 0.001 | 0.02 | 0.04 | 0.06 | 0.08 | 0.1 | 0.117 | 0.118 | 0.118 | 0.118 | 0.118 | 0.118 | 0.118 | 0.118 | 0.118 | 0.118 | 0.118 | 0.118 | 0.118 | 0.118 | 0.118 | 0.118 | 1000
Poussée (en N) | 0 | 310 | 250 | 210 | 180 | 156 | 140 | 125 | 0 | 0 | 0 | 0 | 0 | 0 | 0 | 0 | 0 | 0 | 0 | 0 | 0 | 0 | 0 | 0
I_total_i (en N.s) | 0.2 | 5.3 | 4.6 | 3.9 | 3.4 | 3 | 2.3 | 0.1 | 0 | 0 | 0 | 0 | 0 | 0 | 0 | 0 | 0 | 0 | 0 | 0 | 0 | 0 | 0
H2O 2.0L 1000g 6bar | 61 | I_total | 25.9 N.s | ISP | 2.6 s | MpropuPlein | 1.1 kg | M_éjecté | 1 kg | M_burnout | 0.1 kg | XpropuPlein | 150 mm | XpropuVide | 150 mm | Longueur | 300 mm | Diamètre | 98 mm | Type | H2O
Temps (en s) | 0 | 0.001 | 0.02 | 0.04 | 0.06 | 0.08 | 0.1 | 0.12 | 0.14 | 0.164 | 0.165 | 0.165 | 0.165 | 0.165 | 0.165 | 0.165 | 0.165 | 0.165 | 0.165 | 0.165 | 0.165 | 0.165 | 0.165 | 1000
Poussée (en N) | 0 | 310 | 245 | 200 | 165 | 143 | 124 | 108 | 97 | 85 | 0 | 0 | 0 | 0 | 0 | 0 | 0 | 0 | 0 | 0 | 0 | 0 | 0 | 0
I_total_i (en N.s) | 0.2 | 5.3 | 4.5 | 3.6 | 3.1 | 2.7 | 2.3 | 2.1 | 2.2 | 0.0425 | 0 | 0 | 0 | 0 | 0 | 0 | 0 | 0 | 0 | 0 | 0 | 0 | 0
µ-propu
µ-propu A8-3 | 67 | I_total | 2.6 N.s | ISP | 54.02650357 s | MpropuPlein | 0.015 kg | M_éjecté | 0.005 kg | M_burnout | 0.01 kg | XpropuPlein | 30 mm | XpropuVide | 30 mm | Longueur | 70 mm | Diamètre | 15 mm | Type | Micro | Combustion | 0.32 s | Dépotage | 3
Temps (en s) | 0 | 0.2 | 0.3 | 0.4 | 0.5 | 0.55 | 0.6 | 0.6 | 0.6 | 0.6 | 0.6 | 0.6 | 0.6 | 0.6 | 0.6 | 0.6 | 0.6 | 0.6 | 0.6 | 0.6 | 0.6 | 0.6 | 0.6 | 1000
Poussée (en N) | 0 | 9 | 4.5 | 4 | 4 | 3 | 0 | 0 | 0 | 0 | 0 | 0 | 0 | 0 | 0 | 0 | 0 | 0 | 0 | 0 | 0 | 0 | 0 | 0
I_total_i (en N.s) | 0.9 | 0.7 | 0.4 | 0.4 | 0.2 | 0.1 | 0 | 0 | 0 | 0 | 0 | 0 | 0 | 0 | 0 | 0 | 0 | 0 | 0 | 0 | 0 | 0 | 0
µ-propu B4-4 | 72 | I_total | 5.2 N.s | ISP | 89.19469929 s | MpropuPlein | 0.02 kg | M_éjecté | 0.006 kg | M_burnout | 0.014 kg | XpropuPlein | 30 mm | XpropuVide | 30 mm | Longueur | 70 mm | Diamètre | 15 mm | Type | Micro | Combustion | 1.20 s | Dépotage | 4
Temps (en s) | 0 | 0.2 | 0.3 | 0.55 | 1.05 | 1.15 | 1.15 | 1.15 | 1.15 | 1.15 | 1.15 | 1.15 | 1.15 | 1.15 | 1.15 | 1.15 | 1.15 | 1.15 | 1.15 | 1.15 | 1.15 | 1.15 | 1.15 | 1000
Poussée (en N) | 0 | 10 | 6 | 4 | 4 | 0 | 0 | 0 | 0 | 0 | 0 | 0 | 0 | 0 | 0 | 0 | 0 | 0 | 0 | 0 | 0 | 0 | 0 | 0
I_total_i (en N.s) | 1 | 0.8 | 1.3 | 2 | 0.2 | 0 | 0 | 0 | 0 | 0 | 0 | 0 | 0 | 0 | 0 | 0 | 0 | 0 | 0 | 0 | 0 | 0 | 0
µ-propu C6-3 | 77 | I_total | 10.3 N.s | ISP | 80.45165843 s | MpropuPlein | 0.024 kg | M_éjecté | 0.013 kg | M_burnout | 0.011 kg | XpropuPlein | 30 mm | XpropuVide | 30 mm | Longueur | 70 mm | Diamètre | 15 mm | Type | Micro | Combustion | 1.70 s | Dépotage | 3
Temps (en s) | 0 | 0.2 | 0.3 | 0.6 | 0.8 | 2 | 2.1 | 2.1 | 2.1 | 2.1 | 2.1 | 2.1 | 2.1 | 2.1 | 2.1 | 2.1 | 2.1 | 2.1 | 2.1 | 2.1 | 2.1 | 2.1 | 2.1 | 1000
Poussée (en N) | 0 | 11 | 7 | 4 | 4.6 | 4.6 | 0 | 0 | 0 | 0 | 0 | 0 | 0 | 0 | 0 | 0 | 0 | 0 | 0 | 0 | 0 | 0 | 0 | 0
I_total_i (en N.s) | 1.1 | 0.9 | 1.6 | 0.9 | 5.5 | 0.2 | 0 | 0 | 0 | 0 | 0 | 0 | 0 | 0 | 0 | 0 | 0 | 0 | 0 | 0 | 0 | 0 | 0
µ-propu C6-3 x2 | 82 | I_total | 20.5 N.s | ISP | 80.45165843 s | MpropuPlein | 0.048 kg | M_éjecté | 0.026 kg | M_burnout | 0.022 kg | XpropuPlein | 30 mm | XpropuVide | 30 mm | Longueur | 70 mm | Diamètre | 30 mm | Type | Micro | Combustion | 1.70 s | Dépotage | 3
Temps (en s) | 0 | 0.2 | 0.3 | 0.6 | 0.8 | 2 | 2.1 | 2.1 | 2.1 | 2.1 | 2.1 | 2.1 | 2.1 | 2.1 | 2.1 | 2.1 | 2.1 | 2.1 | 2.1 | 2.1 | 2.1 | 2.1 | 2.1 | 1000
Poussée (en N) | 0 | 22 | 14 | 8 | 9.2 | 9.2 | 0 | 0 | 0 | 0 | 0 | 0 | 0 | 0 | 0 | 0 | 0 | 0 | 0 | 0 | 0 | 0 | 0 | 0
I_total_i (en N.s) | 2.2 | 1.8 | 3.3 | 1.7 | 11 | 0.5 | 0 | 0 | 0 | 0 | 0 | 0 | 0 | 0 | 0 | 0 | 0 | 0 | 0 | 0 | 0 | 0 | 0
µ-propu C6-3 x3 | 87 | I_total | 30.8 N.s | ISP | 80.45165843 s | MpropuPlein | 0.072 kg | M_éjecté | 0.039 kg | M_burnout | 0.033 kg | XpropuPlein | 30 mm | XpropuVide | 30 mm | Longueur | 70 mm | Diamètre | 40 mm | Type | Micro | Combustion | 1.70 s | Dépotage | 3
Temps (en s) | 0 | 0.2 | 0.3 | 0.6 | 0.8 | 2 | 2.1 | 2.1 | 2.1 | 2.1 | 2.1 | 2.1 | 2.1 | 2.1 | 2.1 | 2.1 | 2.1 | 2.1 | 2.1 | 2.1 | 2.1 | 2.1 | 2.1 | 1000
Poussée (en N) | 0 | 33 | 21 | 12 | 13.8 | 13.8 | 0 | 0 | 0 | 0 | 0 | 0 | 0 | 0 | 0 | 0 | 0 | 0 | 0 | 0 | 0 | 0 | 0 | 0
I_total_i (en N.s) | 3.3 | 2.7 | 5 | 2.6 | 16.6 | 0.7 | 0 | 0 | 0 | 0 | 0 | 0 | 0 | 0 | 0 | 0 | 0 | 0 | 0 | 0 | 0 | 0 | 0
MINIF PRO24-1G
p24-1G 24E22 | 93 | I_total | 24.3 N.s | ISP | 154.6223178 s | MpropuPlein | 0.052 kg | M_éjecté | 0.016 kg | M_burnout | 0.036 kg | XpropuPlein | 35.0 mm | XpropuVide | 35.0 mm | Longueur | 69 mm | Diamètre | 24 mm | Type | MiniR | Combustion | 1.00 s | Dépotage | 13
Temps (en s) | 0 | 0.008 | 0.026 | 0.038 | 0.067 | 0.101 | 0.33 | 0.528 | 0.716 | 0.841 | 0.912 | 0.987 | 1.016 | 1.065 | 1.087 | 2 | 2 | 2 | 2 | 2 | 2 | 2 | 2 | 1000
Poussée (en N) | 0 | 18.292 | 30 | 30.792 | 18.708 | 21.875 | 26.083 | 28.042 | 27.875 | 23.542 | 17.833 | 7 | 3.333 | 1.083 | 0 | 0 | 0 | 0 | 0 | 0 | 0 | 0 | 0 | 0
I_total_i (en N.s) | 0.1 | 0.4 | 0.4 | 0.7 | 0.7 | 5.5 | 5.4 | 5.3 | 3.2 | 1.5 | 0.9 | 0.1 | 0.1 | 0.011913 | 0 | 0 | 0 | 0 | 0 | 0 | 0 | 0 | 0
p24-1G 25E75 (Rufina) | 98 | I_total | 24.5 N.s | ISP | 121.7717014 s | MpropuPlein | 0.0565 kg | M_éjecté | 0.0205 kg | M_burnout | 0.036 kg | XpropuPlein | 35.0 mm | XpropuVide | 35.0 mm | Longueur | 69 mm | Diamètre | 24 mm | Type | MiniRN | Combustion | 0.33 s | Dépotage | 17
Temps (en s) | 0 | 0.009 | 0.012 | 0.023 | 0.027 | 0.047 | 0.092 | 0.118 | 0.141 | 0.192 | 0.222 | 0.25 | 0.26 | 0.281 | 0.287 | 0.306 | 0.314 | 0.326 | 0.329 | 0.5 | 1 | 2 | 2 | 1000
Poussée (en N) | 0 | 84.213 | 95.099 | 77.08 | 68.697 | 73.452 | 81.835 | 83.837 | 86.465 | 86.966 | 85.339 | 80.083 | 78.332 | 82.961 | 78.206 | 24.776 | 14.14 | 8.509 | 0 | 0 | 0 | 0 | 0 | 0
I_total_i (en N.s) | 0.4 | 0.3 | 0.9 | 0.3 | 1.4 | 3.5 | 2.2 | 2 | 4.4 | 2.6 | 2.3 | 0.8 | 1.7 | 0.5 | 1 | 0.2 | 0.1 | 0.0127635 | 0 | 0 | 0 | 0 | 0
p24-1G 26E31 | 103 | I_total | 26.1 N.s | ISP | 166.1823554 s | MpropuPlein | 0.052 kg | M_éjecté | 0.016 kg | M_burnout | 0.036 kg | XpropuPlein | 35.0 mm | XpropuVide | 35.0 mm | Longueur | 69 mm | Diamètre | 24 mm | Type | MiniR | Combustion | 0.85 s | Dépotage | 15
Temps (en s) | 0 | 0.02 | 0.027 | 0.049 | 0.113 | 0.193 | 0.282 | 0.5 | 0.727 | 0.771 | 0.807 | 0.84 | 0.87 | 1 | 1 | 1 | 1 | 1 | 1 | 1 | 1 | 1 | 2 | 1000
Poussée (en N) | 0 | 43.824 | 39.964 | 26.781 | 32.601 | 34.739 | 35.808 | 34.442 | 29.276 | 22.743 | 9.561 | 3.563 | 0 | 0 | 0 | 0 | 0 | 0 | 0 | 0 | 0 | 0 | 0 | 0
I_total_i (en N.s) | 0.4 | 0.3 | 0.7 | 1.9 | 2.7 | 3.1 | 7.7 | 7.2 | 1.1 | 0.6 | 0.2 | 0.1 | 0 | 0 | 0 | 0 | 0 | 0 | 0 | 0 | 0 | 0 | 0
MINIF PRO24-2G
p24-2G 50E51 | 108 | I_total | 49.8 N.s | ISP | 231 s | MpropuPlein | 0.073 kg | M_éjecté | 0.028 kg | M_burnout | 0.045 kg | XpropuPlein | 50.0 mm | XpropuVide | 50.0 mm | Longueur | 101 mm | Diamètre | 24 mm | Type | Mini | Combustion | 1.00 s | Dépotage | 13
Temps (en s) | 0 | 0.001 | 0.027 | 0.051 | 0.06 | 0.092 | 0.119 | 0.17 | 0.3 | 0.462 | 0.569 | 0.675 | 0.778 | 0.846 | 0.917 | 1.009 | 1.032 | 1.045 | 2 | 2 | 2 | 2 | 2 | 1000
Poussée (en N) | 0 | 5.145 | 67.976 | 53.807 | 52.88 | 55.916 | 57.94 | 59.711 | 61.145 | 58.952 | 55.578 | 52.205 | 46.386 | 38.12 | 20.325 | 3.542 | 1.602 | 0 | 0 | 0 | 0 | 0 | 0 | 0
I_total_i (en N.s) | 0.0025725 | 1 | 1.5 | 0.5 | 1.7 | 1.5 | 3 | 7.9 | 9.7 | 6.1 | 5.7 | 5.1 | 2.9 | 2.1 | 1.1 | 0.1 | 0.010413 | 0 | 0 | 0 | 0 | 0 | 0
p24-1G 53E70 | 113 | I_total | 52.8 N.s | ISP | 239 s | MpropuPlein | 0.073 kg | M_éjecté | 0.029 kg | M_burnout | 0.044 kg | XpropuPlein | 50.0 mm | XpropuVide | 50.0 mm | Longueur | 101 mm | Diamètre | 24 mm | Type | Mini | Combustion | 0.77 s | Dépotage | 14
Temps (en s) | 0 | 0.001 | 0.013 | 0.023 | 0.052 | 0.1 | 0.379 | 0.641 | 0.665 | 0.706 | 0.744 | 0.787 | 0.816 | 1 | 1 | 1 | 1 | 1 | 1 | 1 | 1 | 2 | 2 | 1000
Poussée (en N) | 0 | 8.303 | 85.68 | 96.149 | 78.821 | 83.634 | 77.858 | 62.575 | 55.716 | 23.947 | 9.146 | 2.768 | 0 | 0 | 0 | 0 | 0 | 0 | 0 | 0 | 0 | 0 | 0 | 0
I_total_i (en N.s) | 0.0041515 | 0.6 | 0.9 | 2.5 | 3.9 | 22.5 | 18.4 | 1.4 | 1.6 | 0.6 | 0.3 | 0.040136 | 0 | 0 | 0 | 0 | 0 | 0 | 0 | 0 | 0 | 0 | 0
MINIF PRO29-1G
p29-1G 41F36 | 118 | I_total | 41.8 N.s | ISP | 121.8435998 s | MpropuPlein | 0.104 kg | M_éjecté | 0.035 kg | M_burnout | 0.069 kg | XpropuPlein | 49 mm | XpropuVide | 49 mm | Longueur | 98 mm | Diamètre | 29 mm | Type | MiniR | Combustion | 1.07 s | Dépotage | 11
Temps (en s) | 0 | 0.01 | 0.02 | 0.03 | 0.04 | 0.06 | 0.07 | 0.08 | 0.1 | 0.2 | 0.3 | 0.4 | 0.5 | 0.6 | 0.7 | 0.8 | 0.85 | 0.92 | 0.95 | 0.99 | 1.05 | 1.05 | 2 | 1000
Poussée (en N) | 0 | 12 | 46 | 75 | 79 | 77 | 62 | 32 | 35 | 38 | 39 | 41 | 43 | 43 | 43 | 43 | 47 | 54 | 32 | 8 | 0 | 0 | 0 | 0
I_total_i (en N.s) | 0.1 | 0.3 | 0.6 | 0.8 | 1.6 | 0.7 | 0.5 | 0.7 | 3.7 | 3.8 | 4 | 4.2 | 4.3 | 4.3 | 4.3 | 2.2 | 3.5 | 1.3 | 0.8 | 0.2 | 0 | 0 | 0
p29-1G 51F36 | 123 | I_total | 52.6 N.s | ISP | 167.4471203 s | MpropuPlein | 0.101 kg | M_éjecté | 0.032 kg | M_burnout | 0.069 kg | XpropuPlein | 49 mm | XpropuVide | 49 mm | Longueur | 98 mm | Diamètre | 29 mm | Type | MiniR | Combustion | 1.80 s | Dépotage | 12
Temps (en s) | 0 | 0.01 | 0.03 | 0.04 | 0.05 | 0.06 | 0.07 | 0.08 | 0.09 | 0.1 | 0.2 | 0.3 | 0.4 | 0.5 | 0.7 | 0.8 | 0.9 | 1 | 1.1 | 1.24 | 1.3 | 1.5 | 2 | 1000
Poussée (en N) | 0 | 12 | 41 | 42 | 42 | 40 | 34 | 34 | 35 | 36 | 40 | 42 | 43 | 43 | 43 | 42 | 41 | 40 | 38 | 37 | 12 | 0 | 0 | 0
I_total_i (en N.s) | 0.1 | 0.5 | 0.4 | 0.4 | 0.4 | 0.4 | 0.3 | 0.3 | 0.4 | 3.8 | 4.1 | 4.3 | 4.3 | 8.6 | 4.3 | 4.1 | 4 | 3.9 | 5.2 | 1.5 | 1.2 | 0 | 0
p29-1G 55F29 | 128 | I_total | 54.1 N.s | ISP | 146.6968576 s | MpropuPlein | 0.1058 kg | M_éjecté | 0.0376 kg | M_burnout | 0.0682 kg | XpropuPlein | 49 mm | XpropuVide | 49 mm | Longueur | 98 mm | Diamètre | 29 mm | Type | MiniR | Combustion | 1.90 s | Dépotage | 12
Temps (en s) | 0 | 0.025 | 0.05 | 0.075 | 0.1 | 0.15 | 0.175 | 0.2 | 0.3 | 0.4 | 0.5 | 0.6 | 0.7 | 0.8 | 0.9 | 1.1 | 1.2 | 1.6 | 1.7 | 1.8 | 1.9 | 1.9999 | 2 | 1000
Poussée (en N) | 0 | 15.26 | 26.38 | 21.48 | 24.02 | 28.11 | 28.69 | 29.18 | 31.49 | 32.56 | 32.83 | 32.65 | 32.38 | 32.25 | 31.80 | 30.56 | 30.07 | 26.38 | 24.87 | 18.46 | 7.52 | 1.38 | 0 | 0
I_total_i (en N.s) | 0.2 | 0.5 | 0.6 | 0.6 | 1.3 | 0.7 | 0.7 | 3 | 3.2 | 3.3 | 3.3 | 3.3 | 3.2 | 3.2 | 6.2 | 3 | 11.3 | 2.6 | 2.2 | 1.3 | 0.4 | 6.894743524e-05 | 0
p29-1G 56F120 | 133 | I_total | 55.7 N.s | ISP | 180.8432981 s | MpropuPlein | 0.1062 kg | M_éjecté | 0.0314 kg | M_burnout | 0.0748 kg | XpropuPlein | 49 mm | XpropuVide | 49 mm | Longueur | 98 mm | Diamètre | 29 mm | Type | MiniRN | Combustion | 0.45 s | Dépotage | 14
Temps (en s) | 0 | 0.013 | 0.017 | 0.04 | 0.125 | 0.179 | 0.222 | 0.289 | 0.354 | 0.394 | 0.406 | 0.416 | 0.423 | 0.431 | 0.447 | 0.453 | 0.455 | 0.455 | 0.455 | 0.455 | 0.455 | 0.455 | 2 | 1000
Poussée (en N) | 0 | 79.242 | 90.427 | 101.422 | 127.583 | 136.114 | 139.905 | 143.507 | 138.578 | 125.498 | 123.602 | 125.118 | 130.047 | 120.569 | 25.592 | 8.72 | 0 | 0 | 0 | 0 | 0 | 0 | 0 | 0
I_total_i (en N.s) | 0.5 | 0.3 | 2.2 | 9.7 | 7.1 | 5.9 | 9.5 | 9.2 | 5.3 | 1.5 | 1.2 | 0.9 | 1 | 1.2 | 0.1 | 0.00872 | 0 | 0 | 0 | 0 | 0 | 0 | 0
p29-1G 57F59 | 138 | I_total | 57.2 N.s | ISP | 188.0569531 s | MpropuPlein | 0.099 kg | M_éjecté | 0.031 kg | M_burnout | 0.068 kg | XpropuPlein | 49 mm | XpropuVide | 49 mm | Longueur | 98 mm | Diamètre | 29 mm | Type | MiniR | Combustion | 0.96 s | Dépotage | 12
Temps (en s) | 0 | 0.01 | 0.02 | 0.03 | 0.04 | 0.07 | 0.1 | 0.2 | 0.3 | 0.4 | 0.5 | 0.6 | 0.7 | 0.87 | 0.9 | 0.97 | 0.97 | 0.97 | 0.97 | 0.97 | 0.97 | 0.97 | 2 | 1000
Poussée (en N) | 0 | 16 | 62 | 67 | 71 | 58 | 63 | 67 | 69 | 67 | 65 | 63 | 61 | 60 | 23 | 0 | 0 | 0 | 0 | 0 | 0 | 0 | 0 | 0
I_total_i (en N.s) | 0.1 | 0.4 | 0.6 | 0.7 | 1.9 | 1.8 | 6.5 | 6.8 | 6.8 | 6.6 | 6.4 | 6.2 | 10.3 | 1.2 | 0.8 | 0 | 0 | 0 | 0 | 0 | 0 | 0 | 0
MINIF PRO24-3G
p24-3G 60F50 | 143 | I_total | 59.7 N.s | ISP | 190.7792477 s | MpropuPlein | 0.0939 kg | M_éjecté | 0.0319 kg | M_burnout | 0.062 kg | XpropuPlein | 66.5 mm | XpropuVide | 66.5 mm | Longueur | 133 mm | Diamètre | 24 mm | Type | MiniR | Combustion | 1.20 s | Dépotage | 13
Temps (en s) | 0 | 0.015 | 0.022 | 0.064 | 0.118 | 0.342 | 0.536 | 0.743 | 0.884 | 0.976 | 1.096 | 1.246 | 1.298 | 2 | 2 | 2 | 2 | 2 | 2 | 2 | 2 | 2 | 2 | 1000
Poussée (en N) | 0 | 64.982 | 69.516 | 55.537 | 62.81 | 62.149 | 59.41 | 53.837 | 46.942 | 40.047 | 12.562 | 2.078 | 0 | 0 | 0 | 0 | 0 | 0 | 0 | 0 | 0 | 0 | 0 | 0
I_total_i (en N.s) | 0.5 | 0.5 | 2.6 | 3.2 | 14 | 11.8 | 11.7 | 7.1 | 4 | 3.2 | 1.1 | 0.1 | 0 | 0 | 0 | 0 | 0 | 0 | 0 | 0 | 0 | 0 | 0
p24-3G 68F79 | 148 | I_total | 68.4 N.s | ISP | 134.048073 s | MpropuPlein | 0.1075 kg | M_éjecté | 0.052 kg | M_burnout | 0.0555 kg | XpropuPlein | 66.5 mm | XpropuVide | 66.5 mm | Longueur | 133 mm | Diamètre | 24 mm | Type | MiniR | Combustion | 0.86 s | Dépotage | 13
Temps (en s) | 0 | 0.005 | 0.013 | 0.022 | 0.043 | 0.119 | 0.198 | 0.267 | 0.343 | 0.404 | 0.498 | 0.555 | 0.622 | 0.663 | 0.704 | 0.729 | 0.747 | 0.768 | 0.821 | 0.852 | 0.892 | 1 | 2 | 1000
Poussée (en N) | 0 | 60 | 89.007 | 96.291 | 81.722 | 85.563 | 87.947 | 89.272 | 89.934 | 90.861 | 91.523 | 89.669 | 83.974 | 80.53 | 78.94 | 74.172 | 66.887 | 53.775 | 18.543 | 7.815 | 2.119 | 0 | 0 | 0
I_total_i (en N.s) | 0.1 | 0.6 | 0.8 | 1.9 | 6.4 | 6.9 | 6.1 | 6.8 | 5.5 | 8.6 | 5.2 | 5.8 | 3.4 | 3.3 | 1.9 | 1.3 | 1.3 | 1.9 | 0.4 | 0.2 | 0.1 | 0 | 0
p24-3G 68F240 | 153 | I_total | 68.0 N.s | ISP | 181.8954586 s | MpropuPlein | 0.0918 kg | M_éjecté | 0.0381 kg | M_burnout | 0.0537 kg | XpropuPlein | 66.5 mm | XpropuVide | 66.5 mm | Longueur | 133 mm | Diamètre | 24 mm | Type | MiniR | Combustion | 0.33 s | Dépotage | 15
Temps (en s) | 0 | 0.004 | 0.007 | 0.01 | 0.022 | 0.028 | 0.041 | 0.058 | 0.077 | 0.089 | 0.097 | 0.119 | 0.147 | 0.177 | 0.207 | 0.253 | 0.259 | 0.272 | 0.28 | 0.286 | 0.294 | 0.328 | 2 | 1000
Poussée (en N) | 0 | 100.53 | 197.49 | 222.03 | 241.43 | 237.86 | 239.45 | 252.51 | 263.98 | 275.46 | 271.50 | 278.63 | 281.40 | 272.30 | 258.44 | 218.47 | 188.79 | 74.80 | 31.27 | 15.83 | 8.71 | 0.00 | 0 | 0
I_total_i (en N.s) | 0.2 | 0.4 | 0.6 | 2.8 | 1.4 | 3.1 | 4.2 | 4.9 | 3.2 | 2.2 | 6.1 | 7.8 | 8.3 | 8 | 11 | 1.2 | 1.7 | 0.4 | 0.1 | 0.1 | 0.1 | 0 | 0
p24-3G 73F30 | 158 | I_total | 73.6 N.s | ISP | 156.866193 s | MpropuPlein | 0.1022 kg | M_éjecté | 0.0478 kg | M_burnout | 0.0544 kg | XpropuPlein | 66.5 mm | XpropuVide | 66.5 mm | Longueur | 133 mm | Diamètre | 24 mm | Type | MiniR | Combustion | 2.36 s | Dépotage | 6
Temps (en s) | 0 | 0.014 | 0.056 | 0.092 | 0.16 | 0.232 | 0.363 | 0.499 | 0.655 | 0.843 | 1.216 | 1.368 | 1.54 | 1.675 | 1.861 | 2.013 | 2.159 | 2.302 | 2.462 | 2.598 | 2.598 | 2.598 | 2.598 | 1000
Poussée (en N) | 0 | 54.22 | 43.46 | 50.19 | 54.06 | 48.36 | 45.75 | 43.14 | 40.29 | 37.84 | 32.61 | 30.32 | 26.36 | 23.51 | 19.08 | 14.56 | 10.05 | 4.83 | 1.50 | 0 | 0 | 0 | 0 | 0
I_total_i (en N.s) | 0.4 | 2.1 | 1.7 | 3.5 | 3.7 | 6.2 | 6 | 6.5 | 7.3 | 13.1 | 4.8 | 4.9 | 3.4 | 4 | 2.6 | 1.8 | 1.1 | 0.5 | 0.1 | 0 | 0 | 0 | 0
p24-3G 74F85 | 163 | I_total | 73.2 N.s | ISP | 177.5872967 s | MpropuPlein | 0.096 kg | M_éjecté | 0.042 kg | M_burnout | 0.054 kg | XpropuPlein | 66.5 mm | XpropuVide | 66.5 mm | Longueur | 133 mm | Diamètre | 24 mm | Type | MiniR | Combustion | 0.87 s | Dépotage | 15
Temps (en s) | 0 | 0.01 | 0.023 | 0.04 | 0.118 | 0.283 | 0.51 | 0.688 | 0.787 | 0.852 | 0.873 | 0.873 | 0.873 | 0.873 | 0.873 | 0.873 | 0.873 | 0.873 | 0.873 | 0.873 | 0.873 | 0.873 | 2 | 1000
Poussée (en N) | 0 | 76.07 | 100.19 | 92.42 | 100.88 | 102.40 | 96.44 | 87.44 | 25.91 | 7.21 | 0 | 0 | 0 | 0 | 0 | 0 | 0 | 0 | 0 | 0 | 0 | 0 | 0 | 0
I_total_i (en N.s) | 0.4 | 1.1 | 1.6 | 7.5 | 16.8 | 22.6 | 16.4 | 5.6 | 1.1 | 0.1 | 0 | 0 | 0 | 0 | 0 | 0 | 0 | 0 | 0 | 0 | 0 | 0 | 0
p24-3G 75F51 | 168 | I_total | 75.3 N.s | ISP | 232.4603342 s | MpropuPlein | 0.095 kg | M_éjecté | 0.033 kg | M_burnout | 0.062 kg | XpropuPlein | 66.5 mm | XpropuVide | 66.5 mm | Longueur | 133 mm | Diamètre | 24 mm | Type | MiniR | Combustion | 1.50 s | Dépotage | 12
Temps (en s) | 0 | 0.02 | 0.031 | 0.062 | 0.117 | 1.211 | 1.376 | 1.456 | 1.532 | 1.577 | 2 | 2 | 2 | 2 | 2 | 2 | 2 | 2 | 2 | 2 | 2 | 2 | 2 | 1000
Poussée (en N) | 0 | 75.924 | 84.148 | 70.441 | 73.659 | 38.737 | 14.779 | 7.271 | 3.337 | 0 | 0 | 0 | 0 | 0 | 0 | 0 | 0 | 0 | 0 | 0 | 0 | 0 | 0 | 0
I_total_i (en N.s) | 0.8 | 0.9 | 2.4 | 4 | 61.5 | 4.4 | 0.9 | 0.4 | 0.1 | 0 | 0 | 0 | 0 | 0 | 0 | 0 | 0 | 0 | 0 | 0 | 0 | 0 | 0
MINIF PRO24-6G
p24-6G 140G145 | 173 | I_total | 141.0 N.s | ISP | 186.2459265 s | MpropuPlein | 0.1619 kg | M_éjecté | 0.0772 kg | M_burnout | 0.0847 kg | XpropuPlein | 114 mm | XpropuVide | 114 mm | Longueur | 228 mm | Diamètre | 24 mm | Type | Mini | Combustion | 0.96 s | Dépotage | 15
Temps (en s) | 0 | 0.02 | 0.03 | 0.05 | 0.6 | 0.67 | 0.7 | 0.8 | 0.9 | 1.05 | 1.05 | 1.05 | 1.05 | 1.05 | 1.05 | 1.05 | 1.05 | 1.05 | 1.05 | 1.05 | 1.05 | 1.05 | 2 | 1000
Poussée (en N) | 0 | 350 | 250 | 210 | 150 | 140 | 130 | 65 | 30 | 0 | 0 | 0 | 0 | 0 | 0 | 0 | 0 | 0 | 0 | 0 | 0 | 0 | 0 | 0
I_total_i (en N.s) | 3.5 | 3 | 4.6 | 99 | 10.2 | 4 | 9.8 | 4.7 | 2.3 | 0 | 0 | 0 | 0 | 0 | 0 | 0 | 0 | 0 | 0 | 0 | 0 | 0 | 0
p24-6G 143G150 | 178 | I_total | 142.4 N.s | ISP | 192.061874 s | MpropuPlein | 0.1599 kg | M_éjecté | 0.0756 kg | M_burnout | 0.0843 kg | XpropuPlein | 114 mm | XpropuVide | 114 mm | Longueur | 228 mm | Diamètre | 24 mm | Type | Mini | Combustion | 0.97 s | Dépotage | 13
Temps (en s) | 0 | 0.02 | 0.04 | 0.62 | 0.66 | 0.68 | 0.8 | 0.84 | 0.88 | 0.92 | 0.96 | 1 | 1.08 | 2 | 2 | 2 | 2 | 2 | 2 | 2 | 2 | 2 | 2 | 1000
Poussée (en N) | 0 | 250 | 210 | 160 | 150 | 142 | 62 | 48 | 34 | 24 | 15 | 10 | 0 | 0 | 0 | 0 | 0 | 0 | 0 | 0 | 0 | 0 | 0 | 0
I_total_i (en N.s) | 2.5 | 4.6 | 107.3 | 6.2 | 2.9 | 12.2 | 2.2 | 1.6 | 1.2 | 0.8 | 0.5 | 0.4 | 0 | 0 | 0 | 0 | 0 | 0 | 0 | 0 | 0 | 0 | 0
p24-6G 139G107 | 183 | I_total | 139.4 N.s | ISP | 158.6202775 s | MpropuPlein | 0.1945 kg | M_éjecté | 0.0896 kg | M_burnout | 0.1049 kg | XpropuPlein | 114 mm | XpropuVide | 144 mm | Longueur | 228 mm | Diamètre | 24 mm | Type | Mini | Combustion | 1.30 s | Dépotage | 12
Temps (en s) | 0 | 0.011 | 0.022 | 0.046 | 0.081 | 0.219 | 0.253 | 0.274 | 0.305 | 0.412 | 0.789 | 0.899 | 0.953 | 0.999 | 1.03 | 1.057 | 1.102 | 1.154 | 1.197 | 1.277 | 1.335 | 1.451 | 2 | 1000
Poussée (en N) | 0 | 198.418 | 221.835 | 212.658 | 218.354 | 204.43 | 195.886 | 183.544 | 88.291 | 93.671 | 93.987 | 91.139 | 89.873 | 87.025 | 81.329 | 69.937 | 54.114 | 42.405 | 31.646 | 17.089 | 9.81 | 0 | 0 | 0
I_total_i (en N.s) | 1.1 | 2.3 | 5.2 | 7.5 | 29.2 | 6.8 | 4 | 4.2 | 9.7 | 35.4 | 10.2 | 4.9 | 4.1 | 2.6 | 2 | 2.8 | 2.5 | 1.6 | 1.9 | 0.8 | 0.6 | 0 | 0
MINIF PRO29-2G
p29-2G 84G88 | 188 | I_total | 82.8 N.s | ISP | 131.8783448 s | MpropuPlein | 0.152 kg | M_éjecté | 0.064 kg | M_burnout | 0.088 kg | XpropuPlein | 71 mm | XpropuVide | 71 mm | Longueur | 142 mm | Diamètre | 29 mm | Type | Mini | Combustion | 0.96 s | Dépotage | 11
Temps (en s) | 0 | 0.02 | 0.03 | 0.04 | 0.06 | 0.08 | 0.15 | 0.18 | 0.2 | 0.3 | 0.4 | 0.5 | 0.6 | 0.7 | 0.82 | 0.93 | 1 | 1 | 1 | 1 | 1 | 1 | 2 | 1000
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

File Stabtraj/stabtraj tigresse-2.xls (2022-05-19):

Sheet: Trajecto
 |  | TRAJECTO
 |  | Trajectographie de fusée
 |  | Remplir les cases jaunes
 |  | Fusée
 | Nom | Tigresse-2
 | Club | Space'Tech Orléans
 | Masse totale | 7.234 kg
 | Propulseur | Barasinga (Pro54-5G)
 |  | Traînée Aérdynamique
 | Surface Réf. | 0.008974 m²
 | Cx | 0.6
 |  | Rampe de Lancement
 | Longueur | 4 m
 | Élévation | 85 °
 | Altitude | 0 m
 |  | DescenteSousParachute |  |  |  | 2022-05-03 | Temps | Altitude z | Portée x | Vitesse | Accélération | Efforts
 |  | Fusée | 0 satellite |  | Sortie de Rampe |  |  |  |  | 29.3 m/s
 | Masse | 6.201 kg | 1 kg |  | Vit max & Acc max |  |  |  |  | 230.2357575 m/s | 113.7910066 m/s²
 | Dépotage | N/A |  |  | Largage du satellite |  | 3.5 s | 511.3072449 m | 54.16323901 m | 225.9830956 m/s |  | 3127.9 N
 | Ouverture para | 18 s | 3.5 s |  | Culmination, Apogée |  | 18.0 s | 1792.922379 m | 295.9835353 m | 13.51956031 m/s
 | Surface para | 2.11 m² | 0.1 m² |  | Ouverture parachute fusée |  | 18.0 s | 1792.922379 m | 295.9835353 m | 13.51956031 m/s |  | 236.5 N
 | Cx parachute | 1 | 1 |  | Impact balistique |  | 40.1 s |  | 519.5586242 m | 127.6 m/s |  | 50506.24062 J
 | Vitesse du vent | 5 m/s | 5 m/s
 | Vitesse descente | 6.9 m/s | 12.7 m/s
 | Durée descente | 261.4854475 s | 40.40177905 s |  |  |  | Pour localiser la fusée
 | Durée du vol | 279.4854475 s | 43.90177905 s |  | Couleur fuselage/coiffe |  | Brun/Orange…
 | Déport latéral | ±1307.427237 m | ±202.0088953 m |  | Couleur parachute fusée |  | Rouge |  |  |  |  |  | fichier initial
 |  |  |  |  | Couleur parachute satellite |  | Jaune |  |  |  |  |  | propu OK
 | Commentaire libre : |  |  |  |  |  |  |  |  |  |  |  | v3.3
Calcul de la surface d'un parachute |  |  |  |  | Résultats détaillés |  | Temps | Altitude z | Portée x | Vitesse | Accélération | Angle
 |  |  |  |  |  |  | s | m | m | m/s | m/s² | °
 |  |  |  |  | Décollage |  | 0 | 0 | 0 | 0 | - | 85
 |  |  |  |  | Sortie de Rampe |  | 0.29 | 3.88 | 0.34 | 29.3 | 108.3 | 85.0
 | Longeur du bord |  |  |  | Vit max & Acc max |  | - | - | - | 230.2357575 | 113.8 | -
 | 650 mm |  |  |  | Fin de Propulsion |  | 3.6 | 533.6119216 | 56.68734521 | 222.8258198 | 34.9 | 83.5
 | Largeur du coté |  |  |  | Culmination, Apogée |  | 18.0 | 1792.922379 | 295.9835353 | 13.51956031 | 9.8 | 2.1
 | 650 mm |  |  |  | Impact balistique |  | 40.1 | ~0 | 519.5586242 | 127.6311416 | 1.2 | -87.5
 | Surface para |  |  |  | Ouverture parachute fusée |  | 18.0 | 1792.922379 | 295.9835353 | 13.51956031 | 9.8 | 2.1
 | 2.11 m² |  |  |  | Impact fusée sous para. |  | 279.4854475 | ~0 | -1011 | 1603 | 6.856681303 | 9.8 | -
 |  |  |  |  | Largage du satellite |  | 3.5 | 511.3072449 | 54.16323901 | 225.9830956 | 27.1 | 83.6
 |  |  |  |  | Impact du satellite |  | 43.90177905 | ~0 | -148 | 256 | 12.65556262 | 9.8 | -
 | Rayon
 | 600 mm
 | Surface para
 | 1.13 m²
 | Vitesse de descente sous parachute :
 | Textes pour les listes déroulantes et graphiques :
 | 0 satellite |  |  |  | N/A | Délais dépotage
 | 1 satellite |  |  |  | -9.0 s | -9
 | Phase ascendante |  |  |  | -7.0 s | -7
 | Descente balistique |  |  |  | -5.0 s | -5
 | Fusée sous parachute |  |  |  | -3.0 s | -3
 |  |  |  |  | 0.0 s | -0
 | Trajectoire (x z) |  |  |  | autre
 | Portée x [m]
 | Temps [s]
 | Altitude z / Temps
 | T_para = | 18
 | Données pour les graphiques :
 | xz max | xz max
 | 1792.922379 | 1792.922379
 | x para | z para
 | 295.9835353 | 1792.922379
 | 295.9835353 | 896.4611894
 | 295.9835353 | 0
 | 340.8065947 | 89.64611894
 | 295.9835353 | 0
 | 251.1604758 | 89.64611894
 | 295.9835353 | 0
 | t para | z para
 | 18.0 | 1792.922379 |  | 1 | vertical
 | 148.7 | 896.4611894 |  | 1 | horizontal
 | 279.5 | 0 |  |  | flèches
 | 277.7 | 37.75834432 |  | 1s | 4.01
 | 279.5 | 0 |  | t/T | 0.94
 | 273.7 | 13.69062237 |  | z/Z | 1.00
 | 279.5 | 0
 | x sat | z sat
 | FALSE | FALSE
 | FALSE | FALSE
 | FALSE | FALSE
 | FALSE | FALSE
 | FALSE | FALSE
 | FALSE | FALSE
 | FALSE | FALSE
 | t sat | z sat
 | FALSE | FALSE
 | 0.0 | 0
 | FALSE | FALSE
 | FALSE | FALSE
 | FALSE | FALSE |  | t/T | 0.91
 | FALSE | FALSE |  | z/Z | 0.91
 | FALSE | FALSE
 | t | z | x
 | 4.5 | 896.4611894 | 73.99588382
 | 29.05 | 896.4611894 | 445.0335945
 | z_triomphe | x_triomphe | Arc de triomphe |  | Arc de triomphe
 | #N/A | 0 | 295.9835353 |  | 295.9835353
 | #N/A | 23 | 318.9835353 |  | 272.9835353
 | #N/A | 23 | 318.9835353 |  | 272.9835353
 | #N/A | 0 | 295.9835353 |  | 295.9835353
 | #N/A | 23 | 318.9835353 |  | 272.9835353
 | #N/A | 23 | 318.9835353 |  | 272.9835353
 | #N/A | 8 | 303.9835353 |  | 287.9835353
 | #N/A | 8 | 303.9835353 |  | 287.9835353
 | #N/A | 23 | 318.9835353 |  | 272.9835353
 | #N/A | 8 | 303.9835353 |  | 287.9835353
 | #N/A | 7.6 | 303.5835353 |  | 288.3835353
 | #N/A | 6.8 | 302.7835353 |  | 289.1835353
 | #N/A | 6 | 301.9835353 |  | 289.9835353
 | #N/A | 5 | 300.9835353 |  | 290.9835353
 | #N/A | 3.8 | 299.7835353 |  | 292.1835353
 | #N/A | 0 | 295.9835353 |  | 295.9835353
 | z_Eiffel | x_Eiffel | Tour Eiffel |  | Tour Eiffel
 | 324 | 0 | 295.9835353 |  | 295.9835353
 | 300 | 0 | 295.9835353 |  | 295.9835353
 | 280 | 10 | 305.9835353 |  | 285.9835353
 | 280 | 0 | 295.9835353 |  | 295.9835353
 | 280 | 10 | 305.9835353 |  | 285.9835353
 | 200 | 13 | 308.9835353 |  | 282.9835353
 | 160 | 17 | 312.9835353 |  | 278.9835353
 | 115 | 20 | 315.9835353 |  | 275.9835353
 | 90 | 25 | 320.9835353 |  | 270.9835353
 | 57 | 30 | 325.9835353 |  | 265.9835353
 | 40 | 36 | 331.9835353 |  | 259.9835353
 | 20 | 48 | 343.9835353 |  | 247.9835353
 | 0.5 | 62 | 357.9835353 |  | 233.9835353
 | 0.5 | 37 | 332.9835353 |  | 258.9835353
 | 15 | 30 | 325.9835353 |  | 265.9835353
 | 30 | 15 | 310.9835353 |  | 280.9835353
 | 37 | 0 | 295.9835353 |  | 295.9835353
 | 67 | 0 | 295.9835353 |  | 295.9835353
 | 67 | 17 | 312.9835353 |  | 278.9835353
 | 100 | 11 | 306.9835353 |  | 284.9835353
 | 100 | 0 | 295.9835353 |  | 295.9835353

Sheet: Propu
Moteur sélectionné | Ligne
Barasinga (Pro54-5G) | 254 | I_total | 2058.4 N.s | ISP | 203.1206673 s | MpropuPlein | 1.685 kg | m_poudre | 1.033 kg | MpropuVide | 0.652 kg | XpropuPlein | 250 mm | XpropuVide | 240 mm | Longueur | 488 mm | Diamètre | 54 mm | Type | Fusex | Combustion | 0.0 s | Dépotage | 0
Temps (en s) | 0 | 0.05 | 0.5 | 1 | 1.5 | 2 | 2.5 | 2.97 | 3.2 | 3.47 | 3.59 | 3.59 | 3.59 | 3.59 | 3.59 | 3.59 | 3.59 | 3.59 | 3.59 | 3.59 | 3.59 | 3.59 | 3.59 | 1000
Poussée (en N) | 0 | 893 | 798 | 739 | 659 | 586 | 513 | 417 | 225 | 67 | 0 | 0 | 0 | 0 | 0 | 0 | 0 | 0 | 0 | 0 | 0 | 0 | 0 | 0
H2O
H2O 1.5L 300g 6bar | 26 | I_total | 9.8 N.s | ISP | 3.3 s | MpropuPlein | 0.3 kg | M_éjecté | 0.3 kg | M_burnout | 0 kg | XpropuPlein | 60 mm | XpropuVide | 150 mm | Longueur | 300 mm | Diamètre | 90 mm | Type | H2O
Temps (en s) | 0 | 0.001 | 0.02 | 0.038 | 0.04 | 0.04 | 0.04 | 0.04 | 0.04 | 0.04 | 0.04 | 0.04 | 0.04 | 0.04 | 0.04 | 0.04 | 0.04 | 0.04 | 0.04 | 0.04 | 0.04 | 0.04 | 0.04 | 1000
Poussée (en N) | 0 | 310 | 250 | 212 | 0 | 0 | 0 | 0 | 0 | 0 | 0 | 0 | 0 | 0 | 0 | 0 | 0 | 0 | 0 | 0 | 0 | 0 | 0 | 0
I_total_i (en N.s) | 0.2 | 5.3 | 4.2 | 0.2 | 0 | 0 | 0 | 0 | 0 | 0 | 0 | 0 | 0 | 0 | 0 | 0 | 0 | 0 | 0 | 0 | 0 | 0 | 0
H2O 1.5L 450g 6bar | 31 | I_total | 13.8 N.s | ISP | 3.1 s | MpropuPlein | 0.45 kg | M_éjecté | 0.45 kg | M_burnout | 0 kg | XpropuPlein | 90 mm | XpropuVide | 150 mm | Longueur | 300 mm | Diamètre | 90 mm | Type | H2O
Temps (en s) | 0 | 0.001 | 0.02 | 0.04 | 0.061 | 0.062 | 0.062 | 0.062 | 0.062 | 0.062 | 0.062 | 0.062 | 0.062 | 0.062 | 0.062 | 0.062 | 0.062 | 0.062 | 0.062 | 0.062 | 0.062 | 0.062 | 0.062 | 1000
Poussée (en N) | 0 | 310 | 245 | 200 | 167 | 0 | 0 | 0 | 0 | 0 | 0 | 0 | 0 | 0 | 0 | 0 | 0 | 0 | 0 | 0 | 0 | 0 | 0 | 0
I_total_i (en N.s) | 0.2 | 5.3 | 4.5 | 3.9 | 0.1 | 0 | 0 | 0 | 0 | 0 | 0 | 0 | 0 | 0 | 0 | 0 | 0 | 0 | 0 | 0 | 0 | 0 | 0
H2O 1.5L 600g 6bar | 36 | I_total | 17.1 N.s | ISP | 2.9 s | MpropuPlein | 0.6 kg | M_éjecté | 0.6 kg | M_burnout | 0 kg | XpropuPlein | 120 mm | XpropuVide | 150 mm | Longueur | 300 mm | Diamètre | 90 mm | Type | H2O
Temps (en s) | 0 | 0.001 | 0.02 | 0.04 | 0.06 | 0.08 | 0.088 | 0.089 | 0.089 | 0.089 | 0.089 | 0.089 | 0.089 | 0.089 | 0.089 | 0.089 | 0.089 | 0.089 | 0.089 | 0.089 | 0.089 | 0.089 | 0.089 | 1000
Poussée (en N) | 0 | 310 | 240 | 190 | 157 | 133 | 125 | 0 | 0 | 0 | 0 | 0 | 0 | 0 | 0 | 0 | 0 | 0 | 0 | 0 | 0 | 0 | 0 | 0
I_total_i (en N.s) | 0.2 | 5.2 | 4.3 | 3.5 | 2.9 | 1 | 0.1 | 0 | 0 | 0 | 0 | 0 | 0 | 0 | 0 | 0 | 0 | 0 | 0 | 0 | 0 | 0 | 0
H2O 1.5L 750g 6bar | 41 | I_total | 19.4 N.s | ISP | 2.6 s | MpropuPlein | 0.75 kg | M_éjecté | 0.75 kg | M_burnout | 0 kg | XpropuPlein | 150 mm | XpropuVide | 150 mm | Longueur | 300 mm | Diamètre | 90 mm | Type | H2O
Temps (en s) | 0 | 0.001 | 0.02 | 0.04 | 0.06 | 0.08 | 0.1 | 0.123 | 0.124 | 0.124 | 0.124 | 0.124 | 0.124 | 0.124 | 0.124 | 0.124 | 0.124 | 0.124 | 0.124 | 0.124 | 0.124 | 0.124 | 0.124 | 1000
Poussée (en N) | 0 | 310 | 230 | 175 | 140 | 118 | 100 | 85 | 0 | 0 | 0 | 0 | 0 | 0 | 0 | 0 | 0 | 0 | 0 | 0 | 0 | 0 | 0 | 0
I_total_i (en N.s) | 0.2 | 5.1 | 4 | 3.1 | 2.6 | 2.2 | 2.1 | 0.0425 | 0 | 0 | 0 | 0 | 0 | 0 | 0 | 0 | 0 | 0 | 0 | 0 | 0 | 0 | 0
H2O 2.0L 400g 6bar | 46 | I_total | 12.9 N.s | ISP | 3.3 s | MpropuPlein | 0.5 kg | M_éjecté | 0.4 kg | M_burnout | 0.1 kg | XpropuPlein | 60 mm | XpropuVide | 150 mm | Longueur | 300 mm | Diamètre | 98 mm | Type | H2O
Temps (en s) | 0 | 0.001 | 0.02 | 0.04 | 0.05 | 0.051 | 0.051 | 0.051 | 0.051 | 0.051 | 0.051 | 0.051 | 0.051 | 0.051 | 0.051 | 0.051 | 0.051 | 0.051 | 0.051 | 0.051 | 0.051 | 0.051 | 0.051 | 1000
Poussée (en N) | 0 | 310 | 264 | 230 | 213 | 0 | 0 | 0 | 0 | 0 | 0 | 0 | 0 | 0 | 0 | 0 | 0 | 0 | 0 | 0 | 0 | 0 | 0 | 0
I_total_i (en N.s) | 0.2 | 5.5 | 4.9 | 2.2 | 0.1 | 0 | 0 | 0 | 0 | 0 | 0 | 0 | 0 | 0 | 0 | 0 | 0 | 0 | 0 | 0 | 0 | 0 | 0
H2O 2.0L 600g 6bar | 51 | I_total | 18.1 N.s | ISP | 3.1 s | MpropuPlein | 0.7 kg | M_éjecté | 0.6 kg | M_burnout | 0.1 kg | XpropuPlein | 90 mm | XpropuVide | 150 mm | Longueur | 300 mm | Diamètre | 98 mm | Type | H2O
Temps (en s) | 0 | 0.001 | 0.02 | 0.04 | 0.06 | 0.08 | 0.081 | 0.081 | 0.081 | 0.081 | 0.081 | 0.081 | 0.081 | 0.081 | 0.081 | 0.081 | 0.081 | 0.081 | 0.081 | 0.081 | 0.081 | 0.081 | 0.081 | 1000
Poussée (en N) | 0 | 310 | 260 | 220 | 190 | 167 | 0 | 0 | 0 | 0 | 0 | 0 | 0 | 0 | 0 | 0 | 0 | 0 | 0 | 0 | 0 | 0 | 0 | 0
I_total_i (en N.s) | 0.2 | 5.4 | 4.8 | 4.1 | 3.6 | 0.1 | 0 | 0 | 0 | 0 | 0 | 0 | 0 | 0 | 0 | 0 | 0 | 0 | 0 | 0 | 0 | 0 | 0
H2O 2.0L 800g 6bar | 56 | I_total | 22.6 N.s | ISP | 2.9 s | MpropuPlein | 0.9 kg | M_éjecté | 0.8 kg | M_burnout | 0.1 kg | XpropuPlein | 120 mm | XpropuVide | 150 mm | Longueur | 300 mm | Diamètre | 98 mm | Type | H2O
Temps (en s) | 0 | 0.001 | 0.02 | 0.04 | 0.06 | 0.08 | 0.1 | 0.117 | 0.118 | 0.118 | 0.118 | 0.118 | 0.118 | 0.118 | 0.118 | 0.118 | 0.118 | 0.118 | 0.118 | 0.118 | 0.118 | 0.118 | 0.118 | 1000
Poussée (en N) | 0 | 310 | 250 | 210 | 180 | 156 | 140 | 125 | 0 | 0 | 0 | 0 | 0 | 0 | 0 | 0 | 0 | 0 | 0 | 0 | 0 | 0 | 0 | 0
I_total_i (en N.s) | 0.2 | 5.3 | 4.6 | 3.9 | 3.4 | 3 | 2.3 | 0.1 | 0 | 0 | 0 | 0 | 0 | 0 | 0 | 0 | 0 | 0 | 0 | 0 | 0 | 0 | 0
H2O 2.0L 1000g 6bar | 61 | I_total | 25.9 N.s | ISP | 2.6 s | MpropuPlein | 1.1 kg | M_éjecté | 1 kg | M_burnout | 0.1 kg | XpropuPlein | 150 mm | XpropuVide | 150 mm | Longueur | 300 mm | Diamètre | 98 mm | Type | H2O
Temps (en s) | 0 | 0.001 | 0.02 | 0.04 | 0.06 | 0.08 | 0.1 | 0.12 | 0.14 | 0.164 | 0.165 | 0.165 | 0.165 | 0.165 | 0.165 | 0.165 | 0.165 | 0.165 | 0.165 | 0.165 | 0.165 | 0.165 | 0.165 | 1000
Poussée (en N) | 0 | 310 | 245 | 200 | 165 | 143 | 124 | 108 | 97 | 85 | 0 | 0 | 0 | 0 | 0 | 0 | 0 | 0 | 0 | 0 | 0 | 0 | 0 | 0
I_total_i (en N.s) | 0.2 | 5.3 | 4.5 | 3.6 | 3.1 | 2.7 | 2.3 | 2.1 | 2.2 | 0.0425 | 0 | 0 | 0 | 0 | 0 | 0 | 0 | 0 | 0 | 0 | 0 | 0 | 0
µ-propu
µ-propu A8-3 | 67 | I_total | 2.6 N.s | ISP | 54.02650357 s | MpropuPlein | 0.015 kg | M_éjecté | 0.005 kg | M_burnout | 0.01 kg | XpropuPlein | 30 mm | XpropuVide | 30 mm | Longueur | 70 mm | Diamètre | 15 mm | Type | Micro | Combustion | 0.32 s | Dépotage | 3
Temps (en s) | 0 | 0.2 | 0.3 | 0.4 | 0.5 | 0.55 | 0.6 | 0.6 | 0.6 | 0.6 | 0.6 | 0.6 | 0.6 | 0.6 | 0.6 | 0.6 | 0.6 | 0.6 | 0.6 | 0.6 | 0.6 | 0.6 | 0.6 | 1000
Poussée (en N) | 0 | 9 | 4.5 | 4 | 4 | 3 | 0 | 0 | 0 | 0 | 0 | 0 | 0 | 0 | 0 | 0 | 0 | 0 | 0 | 0 | 0 | 0 | 0 | 0
I_total_i (en N.s) | 0.9 | 0.7 | 0.4 | 0.4 | 0.2 | 0.1 | 0 | 0 | 0 | 0 | 0 | 0 | 0 | 0 | 0 | 0 | 0 | 0 | 0 | 0 | 0 | 0 | 0
µ-propu B4-4 | 72 | I_total | 5.2 N.s | ISP | 89.19469929 s | MpropuPlein | 0.02 kg | M_éjecté | 0.006 kg | M_burnout | 0.014 kg | XpropuPlein | 30 mm | XpropuVide | 30 mm | Longueur | 70 mm | Diamètre | 15 mm | Type | Micro | Combustion | 1.20 s | Dépotage | 4
Temps (en s) | 0 | 0.2 | 0.3 | 0.55 | 1.05 | 1.15 | 1.15 | 1.15 | 1.15 | 1.15 | 1.15 | 1.15 | 1.15 | 1.15 | 1.15 | 1.15 | 1.15 | 1.15 | 1.15 | 1.15 | 1.15 | 1.15 | 1.15 | 1000
Poussée (en N) | 0 | 10 | 6 | 4 | 4 | 0 | 0 | 0 | 0 | 0 | 0 | 0 | 0 | 0 | 0 | 0 | 0 | 0 | 0 | 0 | 0 | 0 | 0 | 0
I_total_i (en N.s) | 1 | 0.8 | 1.3 | 2 | 0.2 | 0 | 0 | 0 | 0 | 0 | 0 | 0 | 0 | 0 | 0 | 0 | 0 | 0 | 0 | 0 | 0 | 0 | 0
µ-propu C6-3 | 77 | I_total | 10.3 N.s | ISP | 80.45165843 s | MpropuPlein | 0.024 kg | M_éjecté | 0.013 kg | M_burnout | 0.011 kg | XpropuPlein | 30 mm | XpropuVide | 30 mm | Longueur | 70 mm | Diamètre | 15 mm | Type | Micro | Combustion | 1.70 s | Dépotage | 3
Temps (en s) | 0 | 0.2 | 0.3 | 0.6 | 0.8 | 2 | 2.1 | 2.1 | 2.1 | 2.1 | 2.1 | 2.1 | 2.1 | 2.1 | 2.1 | 2.1 | 2.1 | 2.1 | 2.1 | 2.1 | 2.1 | 2.1 | 2.1 | 1000
Poussée (en N) | 0 | 11 | 7 | 4 | 4.6 | 4.6 | 0 | 0 | 0 | 0 | 0 | 0 | 0 | 0 | 0 | 0 | 0 | 0 | 0 | 0 | 0 | 0 | 0 | 0
I_total_i (en N.s) | 1.1 | 0.9 | 1.6 | 0.9 | 5.5 | 0.2 | 0 | 0 | 0 | 0 | 0 | 0 | 0 | 0 | 0 | 0 | 0 | 0 | 0 | 0 | 0 | 0 | 0
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

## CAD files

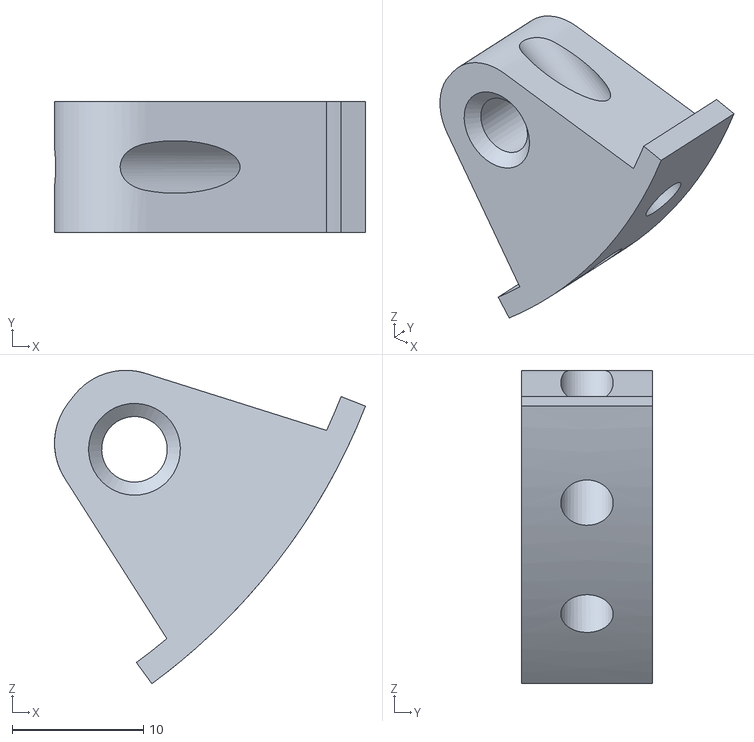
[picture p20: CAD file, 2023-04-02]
Modélisation_3D/Trappe/Maintien_trappe_exp.stl
23.7 x 10.0 x 23.9

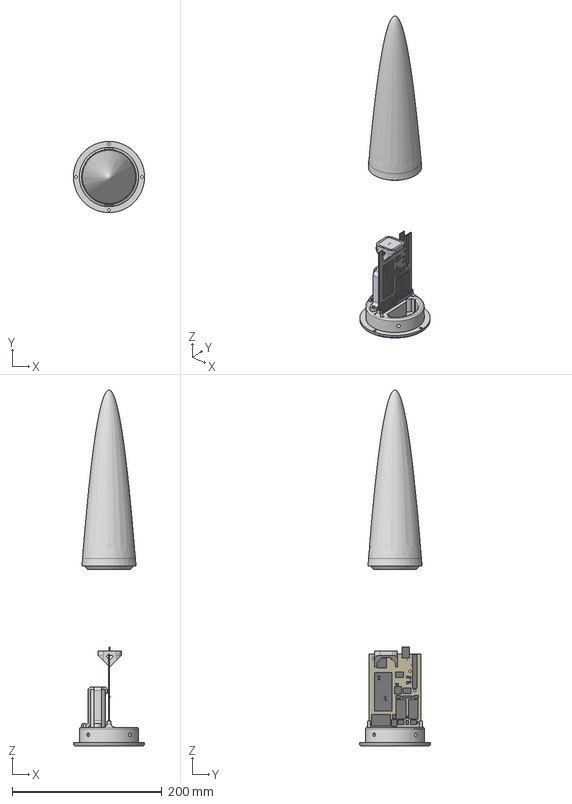
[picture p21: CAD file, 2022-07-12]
Telemetrie/3D parts/assemblage_PCB v21.step
95.0 x 95.0 x 475.0 mm
Board
FEATHER-M0
BMP390
CAPC2012X145N
MAX8Q0
PKMCS
FE06
CONSMA020.042-G
GNSS_ANTENNA
MPU9250_SHIELD
TX3H-869
EEE0GA101SR
CAPC1608X90N x 2
C2012_COMMERCIAL x 2
CAPC4532X250N x 2
RESC1608X55N x 5
TO254P480X1010X2280-3P x 2
SOLDERJUMPER_ARROW_NOPASTE x 4
SOC-23 x 3
VS-30BQ100-M3/9AT x 2
GNSS_ANTENNA_1
SupportGNGG_ANTENNA
NoseConePower
socle_PCB
BAT
bat_holder

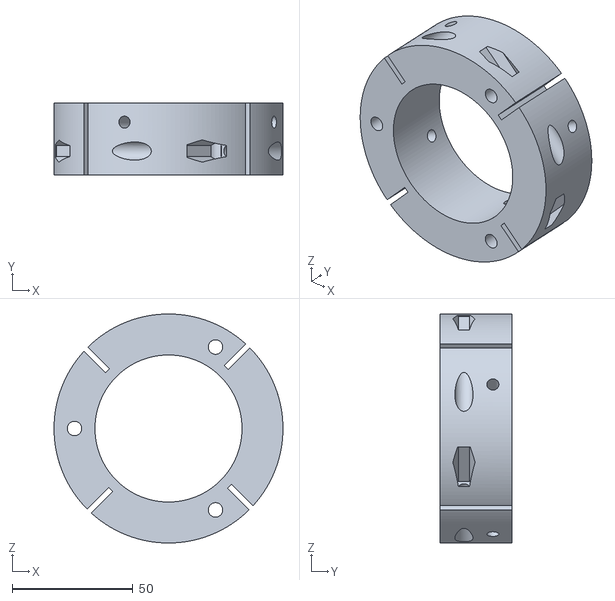
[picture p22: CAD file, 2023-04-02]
Modélisation_3D/Moteur/Bague_avant_maintien_ailerons.stl
95.0 x 30.0 x 95.0

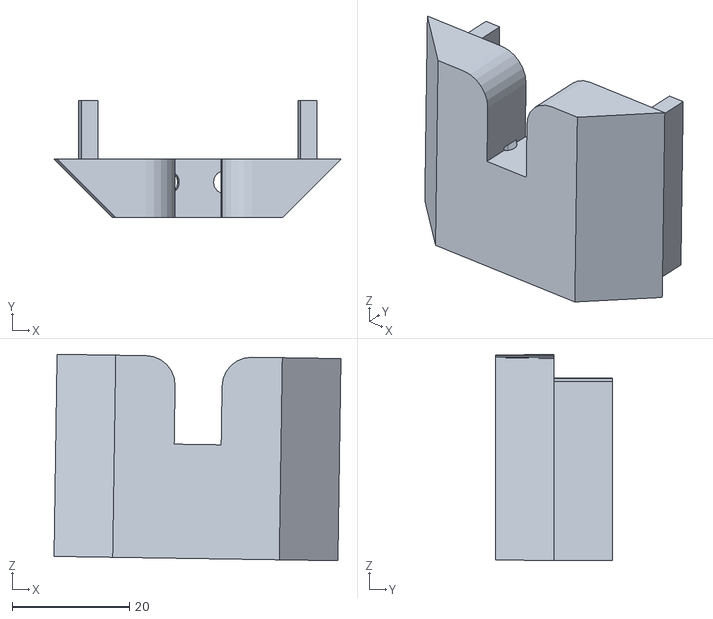
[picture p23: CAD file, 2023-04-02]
Modélisation_3D/Parachute/mecanisme_trappe/Maintien_moteur.stl
48.9 x 20.0 x 35.2

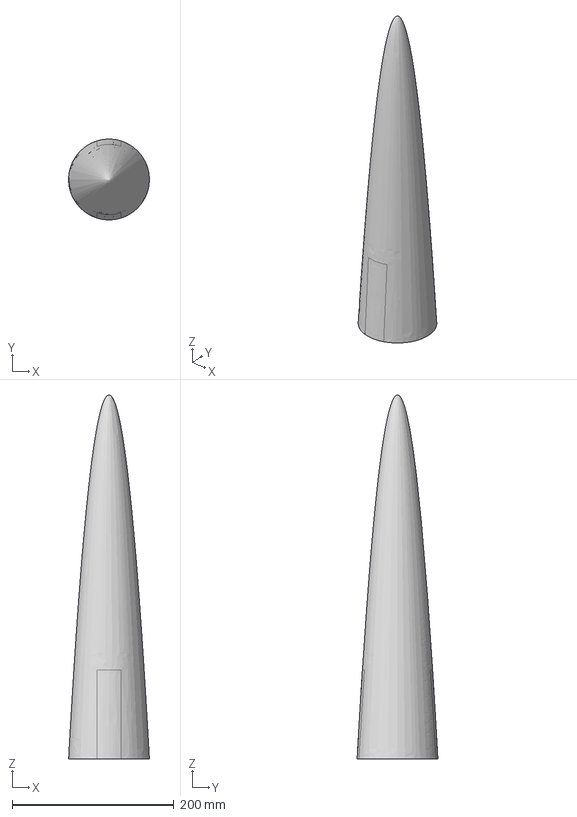
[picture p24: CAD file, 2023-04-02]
Modélisation_3D/Ogive/assemblage_Nose_Cone.step
99.8 x 99.9 x 450.0 mm
Board
FEATHER-M0
BMP390
CAPC2012X145N
MAX8Q0
PKMCS
FE06
CONSMA020.042-G
GNSS_ANTENNA
MPU9250_SHIELD
TX3H-869
EEE0GA101SR
CAPC1608X90N x 2
C2012_COMMERCIAL x 2
CAPC4532X250N x 2
RESC1608X55N x 5
TO254P480X1010X2280-3P x 2
SOLDERJUMPER_ARROW_NOPASTE x 4
SOC-23 x 3
VS-30BQ100-M3/9AT x 2
GNSS_ANTENNA_1
SupportGNGG_ANTENNA
NoseConePower

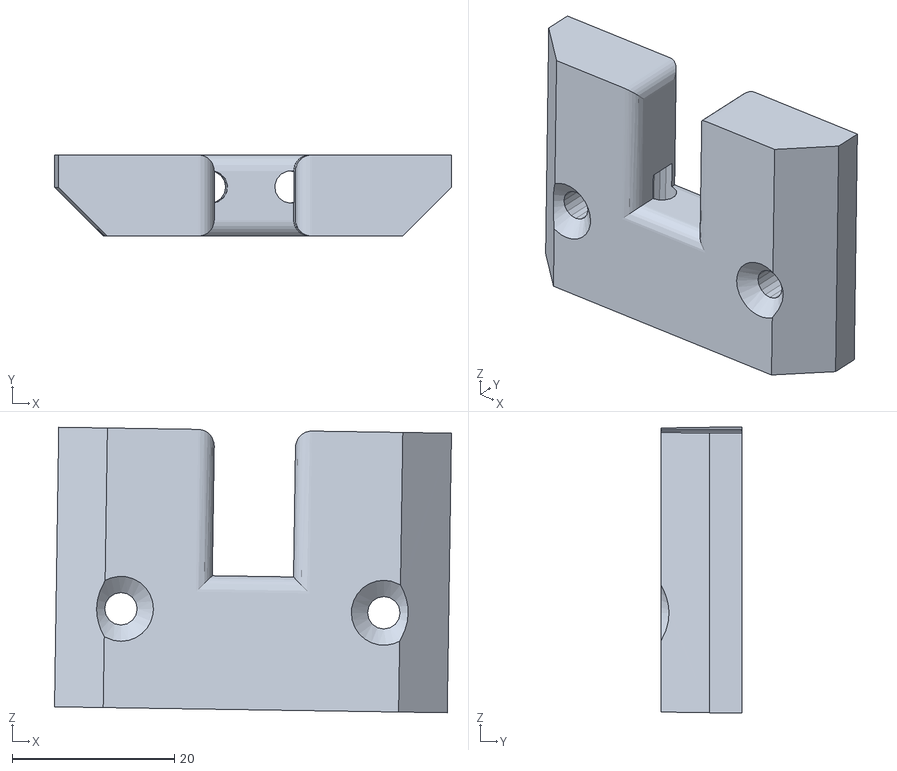
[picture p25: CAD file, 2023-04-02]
Modélisation_3D/Parachute/Maintien_moteur.stl
48.9 x 10.0 x 35.2

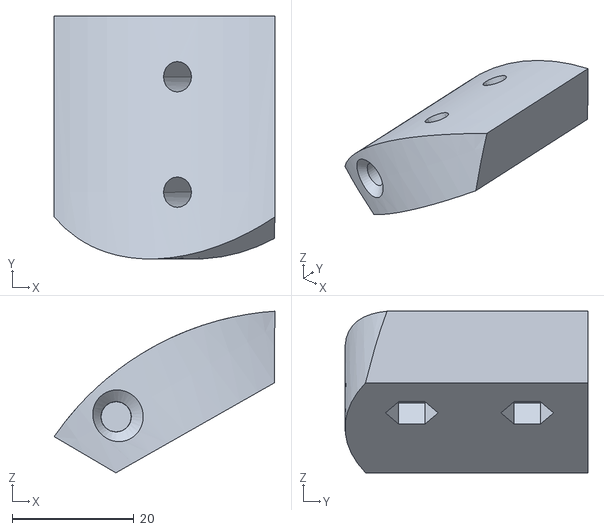
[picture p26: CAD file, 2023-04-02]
Modélisation_3D/Parachute/Maintien_trappe.stl
36.3 x 40.0 x 26.6

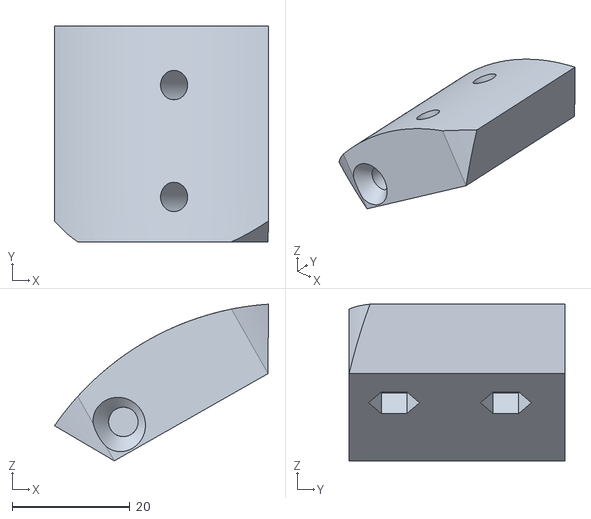
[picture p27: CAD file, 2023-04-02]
Modélisation_3D/Trappe/Maintien_trappe.stl
36.3 x 36.6 x 26.6

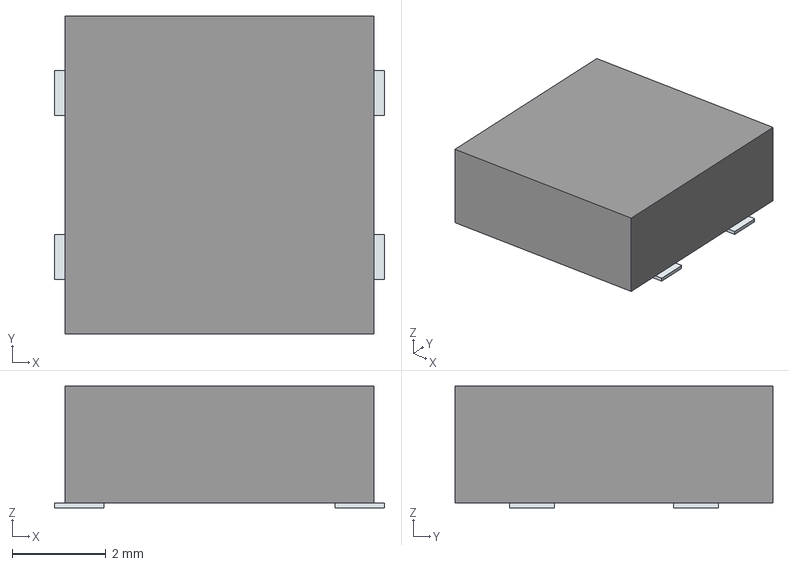
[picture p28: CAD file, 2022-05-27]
Experience/Tigresse_experience v2/CLS62NP-220NC.stp
7.06 x 6.80 x 2.60 mm
Pins

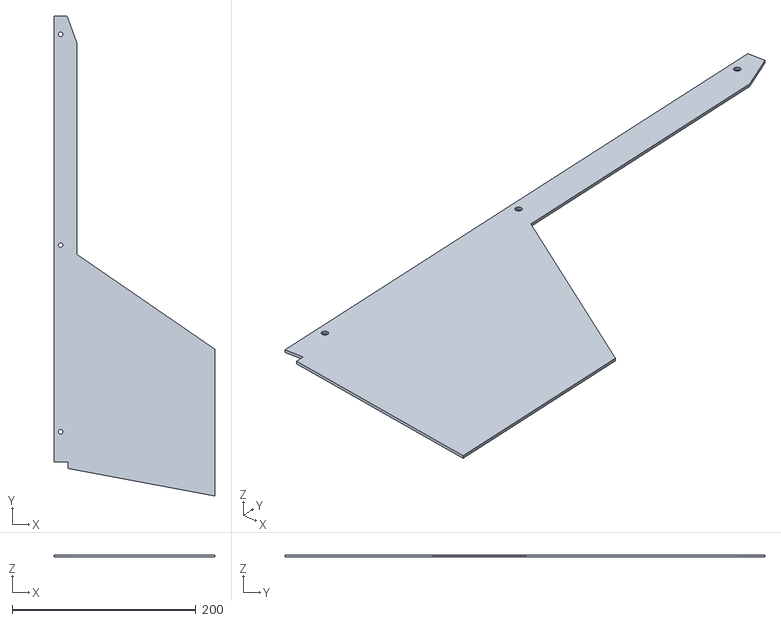
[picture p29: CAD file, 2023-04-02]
Modélisation_3D/Ailerons/Aileron.stl
175.0 x 523.0 x 2.00

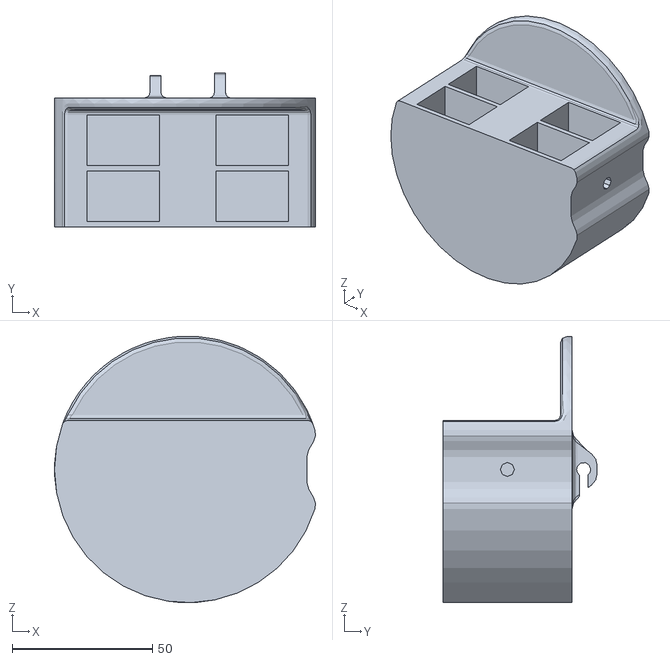
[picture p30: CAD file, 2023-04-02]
Modélisation_3D/Bagues/Bague_antenne/Bague_separation_exp.stl
93.1 x 55.0 x 95.0

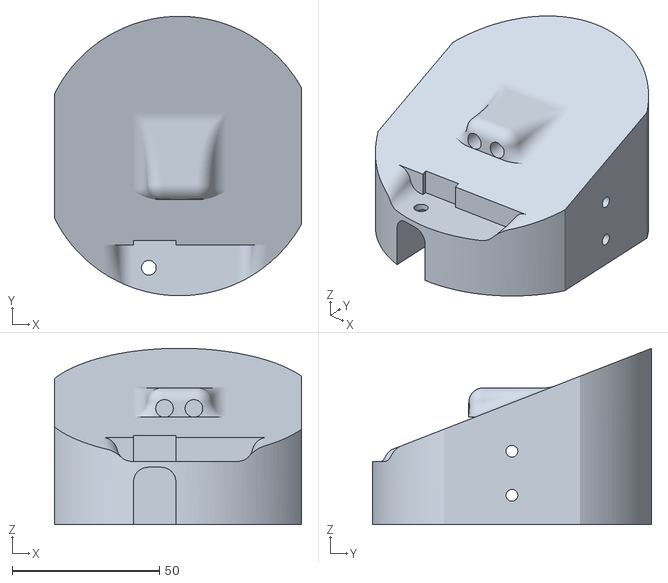
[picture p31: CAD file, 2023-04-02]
Modélisation_3D/Bagues/Bague_IUT_LE_CREUSOT/bague_avant_para.stl
84.0 x 95.0 x 60.0

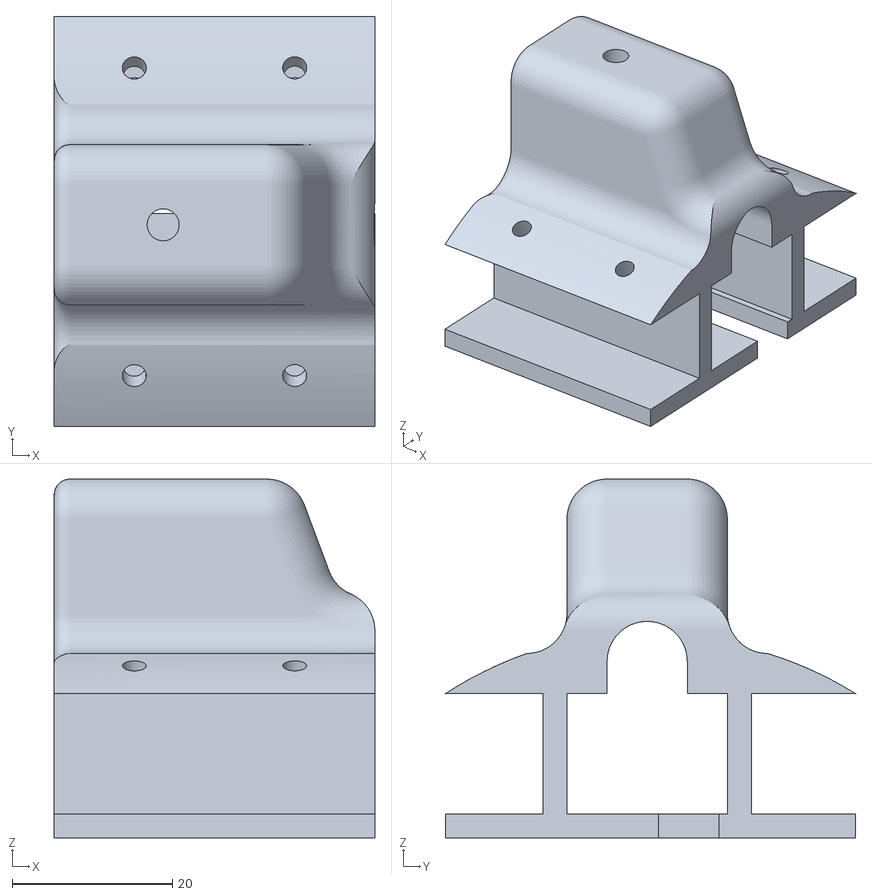
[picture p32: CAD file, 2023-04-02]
Modélisation_3D/Camera/Support_camera.stl
40.0 x 51.1 x 44.7

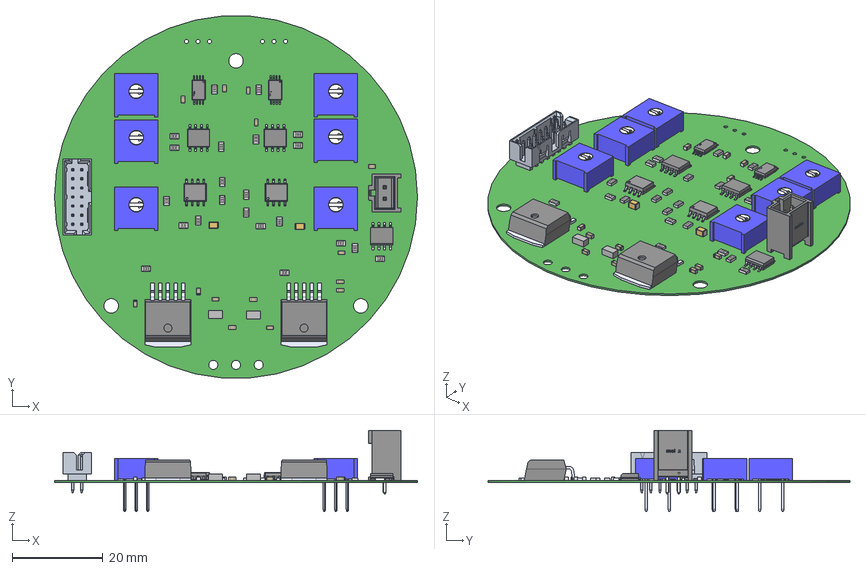
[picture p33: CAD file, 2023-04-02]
Modélisation_3D/CAO_timer/timer_tigresse.step
80.0 x 79.8 x 18.0 mm
LTC1196-1ACS8#PBF
Pin1_Triangle
Molex
RES_0805 x 22
CAP_0603 x 14
Extruded x 2
NCP59301DS50R4G x 2
3386F-1-153LF x 6
IC_BODY x 2
IC_LEG x 8
circle x 2
IC_LEG_MIR7 x 8
Texas_Instruments x 2
MAX4544CSA+ x 2
PinsArrayLR x 2
Open_CASCADE_STEP_translator_6.8_24.1.1 x 2
Open_CASCADE_STEP_translator_6.8_24.1.2 x 2
Open_CASCADE_STEP_translator_6.8_24.2.1 x 2

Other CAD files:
Modélisation_3D/assemblage_PCB-v21.step
Modélisation_3D/Design/tigresse_logo.stl
Modélisation_3D/Energie bord/9V-battery.stp
Experience/Tigresse_experience v2/CLS62NP-220NC.stl
Experience/Tigresse_experience/CLS62NP-220NC.stl
Modélisation_3D/Bagues/Bague_IUT_LE_CREUSOT/Bague_entre_trappe_et _moteur.stl
Modélisation_3D/Bagues/Bague_IUT_LE_CREUSOT/Bague_separation_exp.stl
Modélisation_3D/Bagues/Bague_IUT_LE_CREUSOT/Bague_support_moteur.stl
Modélisation_3D/Bagues/Bague_IUT_LE_CREUSOT/Support_EA.stl
Modélisation_3D/Bagues/Bague_IUT_LE_CREUSOT/Support_EAV1_2.stl
Modélisation_3D/Camera/Support_Runcam_V4.stp
Modélisation_3D/Engrenage_hs422.stl
Modélisation_3D/Fabrication/Bague_trous.stl
Modélisation_3D/Interface/Support_IHM.stl
Modélisation_3D/Interface/interface.step
Modélisation_3D/Moteur/Bague_avant_reprise_moteur.stl
Modélisation_3D/Moteur/Bague_milieu_reprise_moteur.stl
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

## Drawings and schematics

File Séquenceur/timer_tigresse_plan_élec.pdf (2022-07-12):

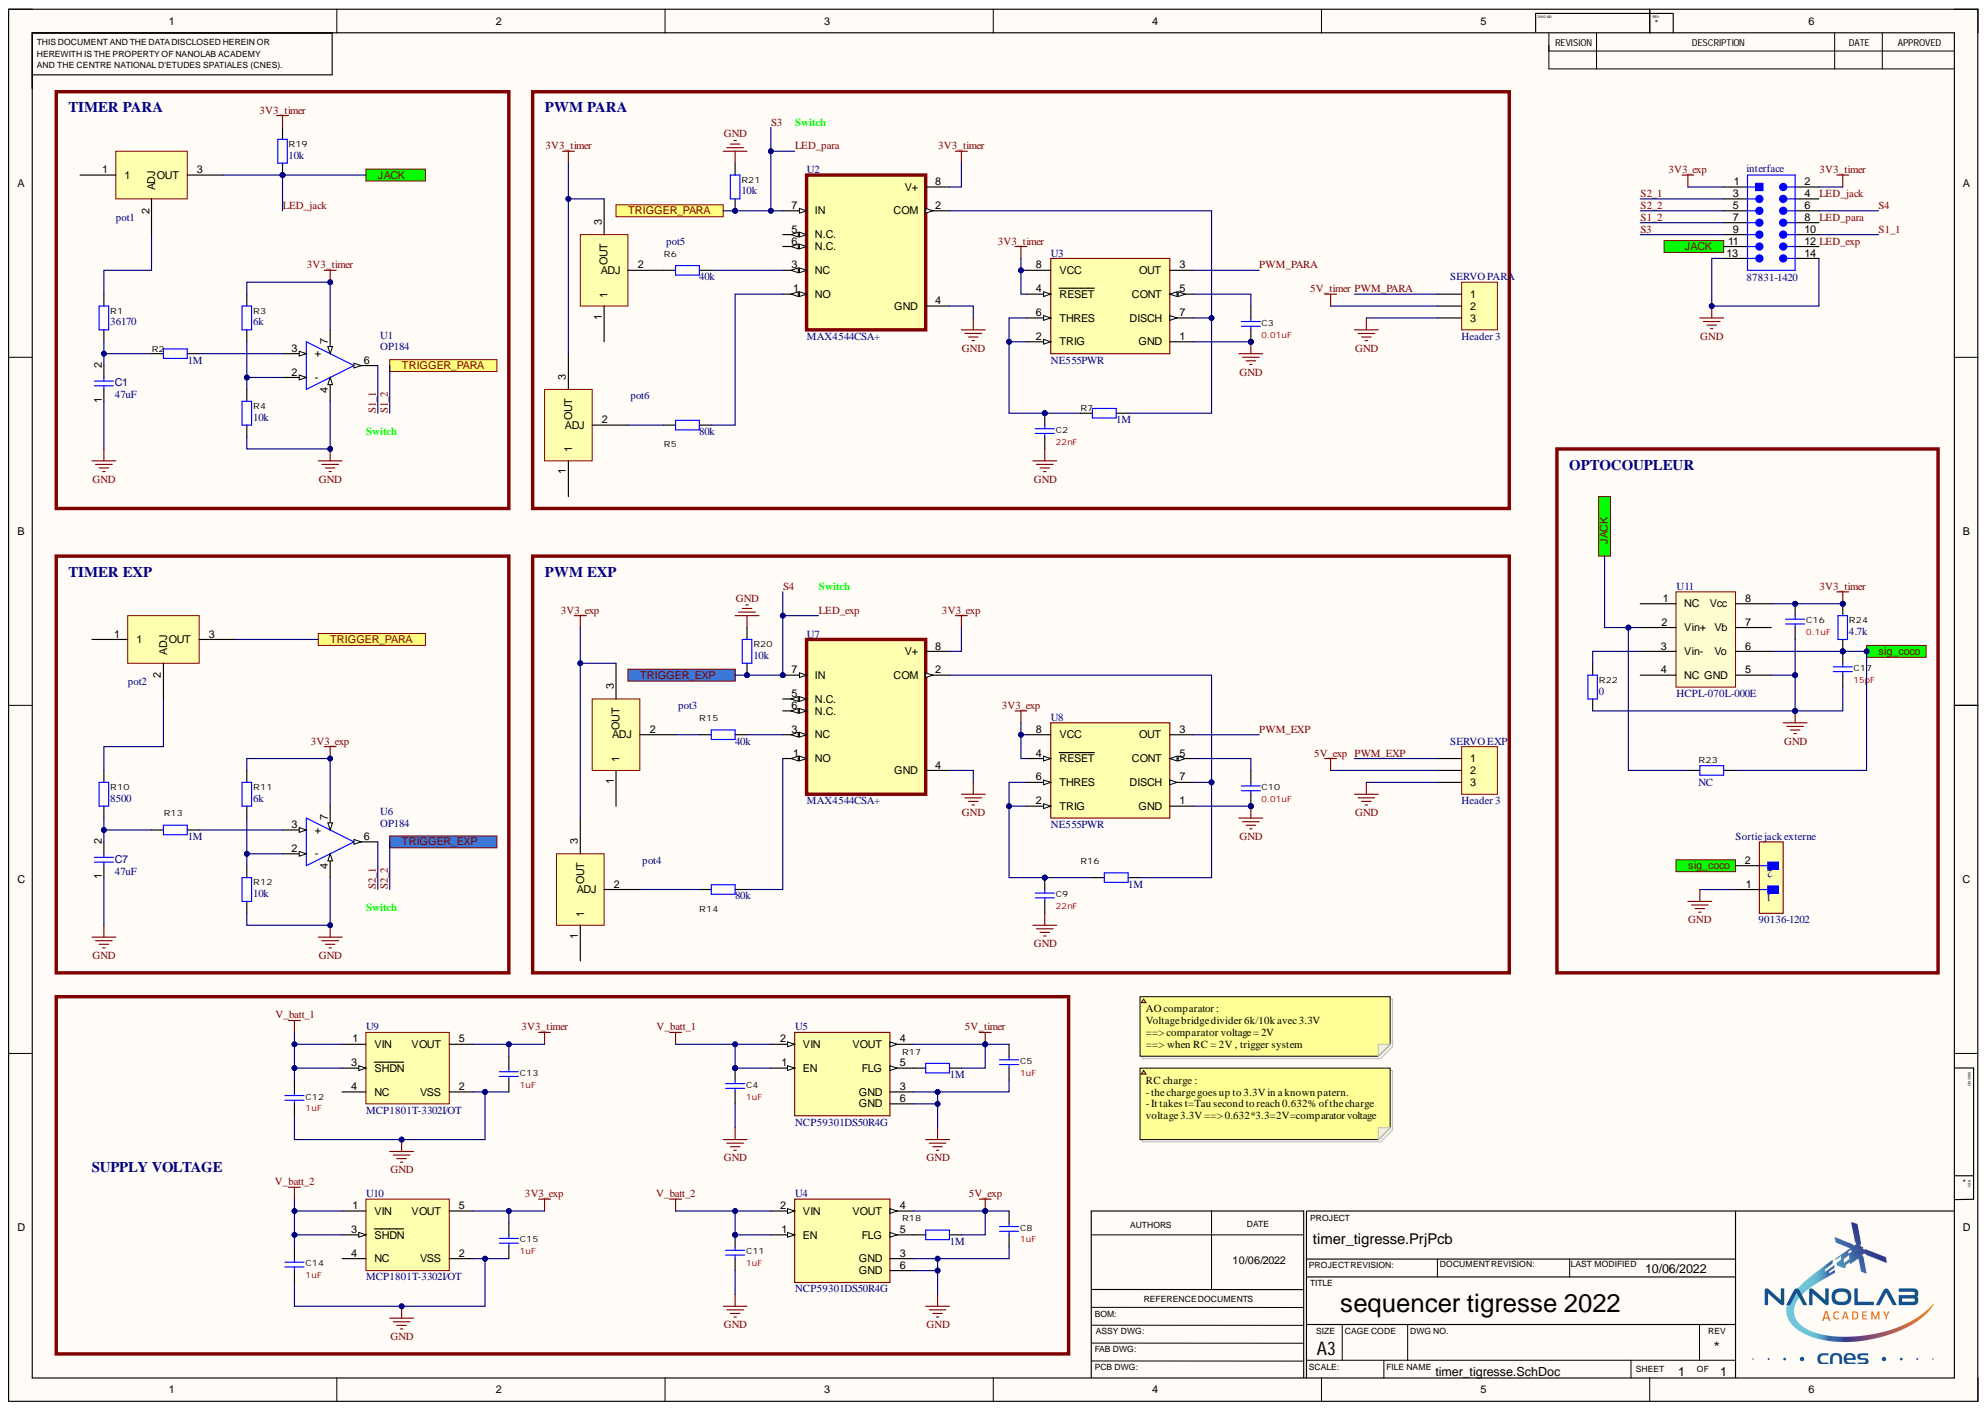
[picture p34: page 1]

1 | 2 | 3 | 4 | 5 | DWG NO: | REV: * | 6

THIS DOCUMENT AND THE DATADISCLOSED HEREIN OR HEREWITH IS THE PROPERTY OF NANOLAB ACADEMY AND THE CENTRE NATIONAL D'ETUDES SPATIALES (CNES). | | REVISION | DESCRIPTION | DATE | APPROVED

Vin- 3

AO comparator :
Voltage bridge divider 6k/10k avec 3.3V
==> comparator voltage= 2V
==> when RC = 2V , trigger system

RC charge :
-the charge goes up to 3.3V in a known patern.
-It takest=Tau second to reach 0.632% ofthe charge
voltage 3.3V ==> 0.632*3.3=2V=comparator voltage

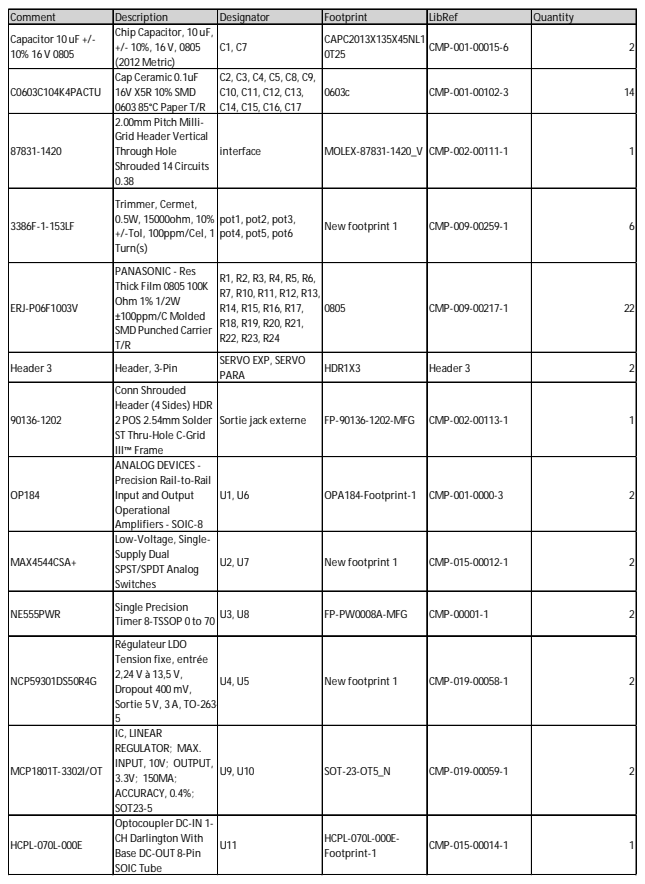
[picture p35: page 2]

Comment | Description | Designator | Footprint | LibRef | Quantity
Capacitor 10 uF +/-10% 16 V 0805 | Chip Capacitor, 10 uF, +/- 10%, 16 V, 0805 (2012 Metric) | C1, C7 | CAPC2013X135X45NL1 0T25 | CMP-001-00015-6 | 2

C0603C104K4PACTU | Cap Ceramic 0.1uF 16V X5R 10% SMD 0603 85°C Paper T/R | C2, C3, C4, C5, C8, C9, C10, C11, C12, C13, C14, C15, C16, C17 | 0603c | CMP-001-00102-3 | 14

87831-1420 | 2.00mm Pitch Milli-Grid Header Vertical Through Hole Shrouded 14 Circuits 0.38 | interface | MOLEX-87831-1420_V | CMP-002-00111-1 | 1

3386F-1-153LF | Trimmer, Cermet, 0.5W, 15000ohm, 10% +/-Tol, 100ppm/Cel, 1 Turn(s) | pot1, pot2, pot3, pot4, pot5, pot6 | New footprint 1 | CMP-009-00259-1 | 6

ERJ-P06F1003V | PANASONIC - Res Thick Film 0805 100K Ohm 1% 1/2W ±100ppm/C Molded SMD Punched Carrier T/R | R1, R2, R3, R4, R5, R6, R7, R10, R11, R12, R13, R14, R15, R16, R17, R18, R19, R20, R21, R22, R23, R24 | 0805 | CMP-009-00217-1 | 22

Header 3 | Header, 3-Pin | SERVO EXP, SERVO PARA | HDR1X3 | Header 3 | 2

90136-1202 | Conn Shrouded Header (4 Sides) HDR 2 POS 2.54mm Solder ST Thru-Hole C-Grid III™ Frame | Sortie jack externe | FP-90136-1202-MFG | CMP-002-00113-1 | 1

OP184 | ANALOG DEVICES -Precision Rail-to-Rail Input and Output Operational Amplifiers - SOIC-8 | U1, U6 | OPA184-Footprint-1 | CMP-001-0000-3 | 2

MAX4544CSA+ | Low-Voltage, Single-Supply Dual SPST/SPDT Analog Switches | U2, U7 | New footprint 1 | CMP-015-00012-1 | 2

NE555PWR | Single Precision Timer 8-TSSOP 0 to 70 | U3, U8 | FP-PW0008A-MFG | CMP-00001-1 | 2

NCP59301DS50R4G | Régulateur LDO Tension fixe, entrée 2,24 V à 13,5 V, Dropout 400mV, Sortie 5 V, 3 A, TO-263-5 | U4, U5 | New footprint 1 | CMP-019-00058-1 | 2

MCP1801T-3302I/OT | IC, LINEAR REGULATOR; MAX. INPUT, 10V; OUTPUT, 3.3V; 150MA; ACCURACY, 0.4%; SOT23-5 | U9, U10 | SOT-23-OT5_N | CMP-019-00059-1 | 2

HCPL-070L-000E | Optocoupler DC-IN 1-CH Darlington With Base DC-OUT 8-Pin SOIC Tube | U11 | HCPL-070L-000E-Footprint-1 | CMP-015-00014-1 | 1

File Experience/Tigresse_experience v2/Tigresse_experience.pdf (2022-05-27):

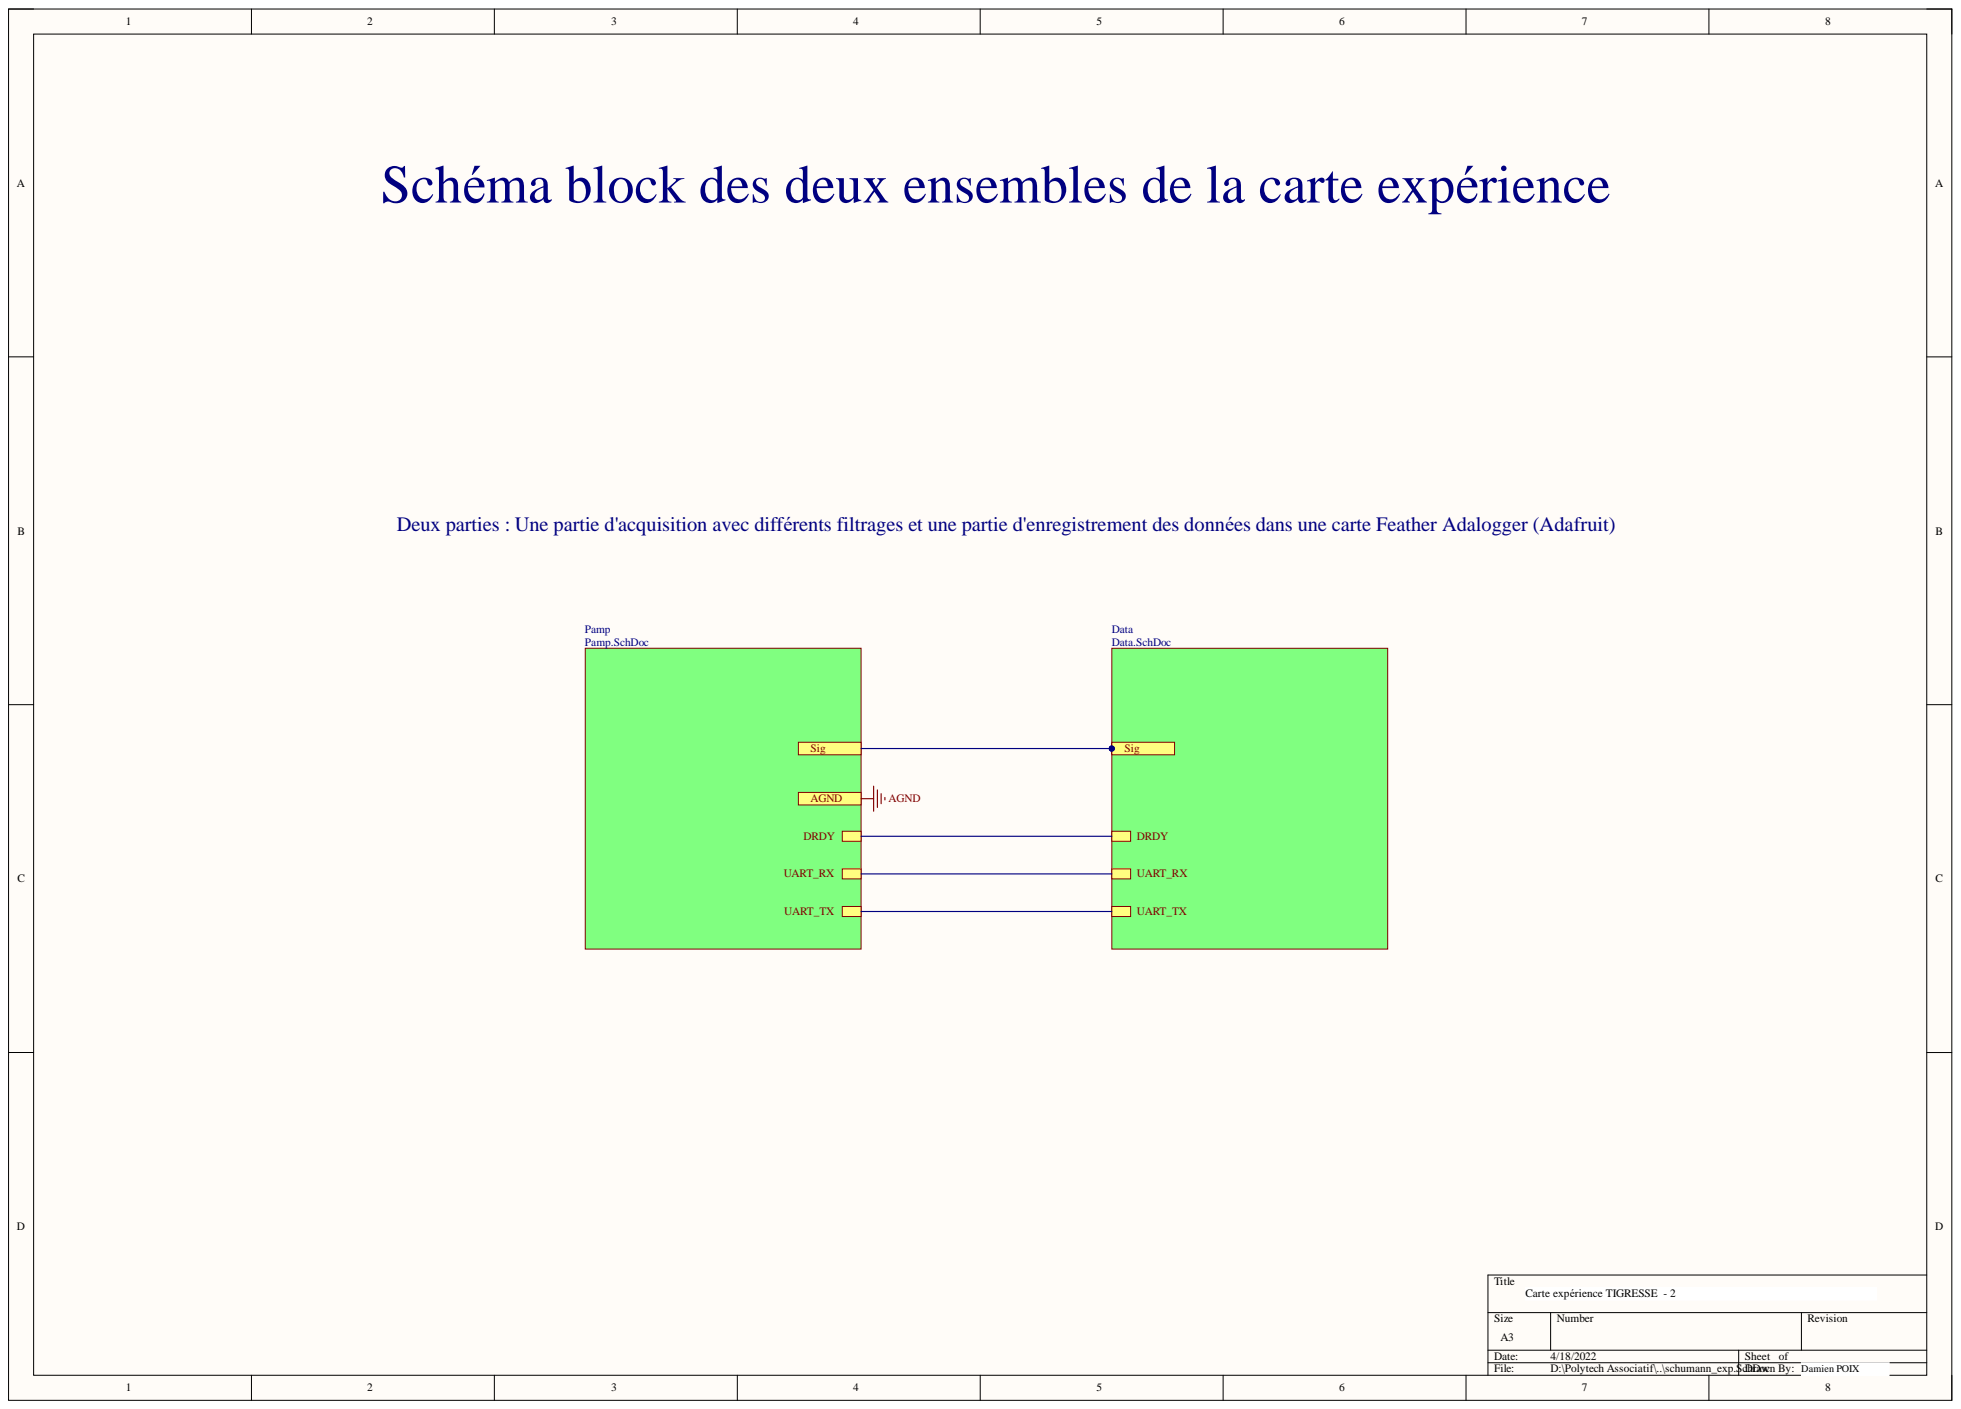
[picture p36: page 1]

Schéma block des deux ensembles de la carte expérience

Deux parties : Une partie d'acquisition avec différents filtrages et une partie d'enregistrement des données dans une carte Feather Adalogger (Adafruit)

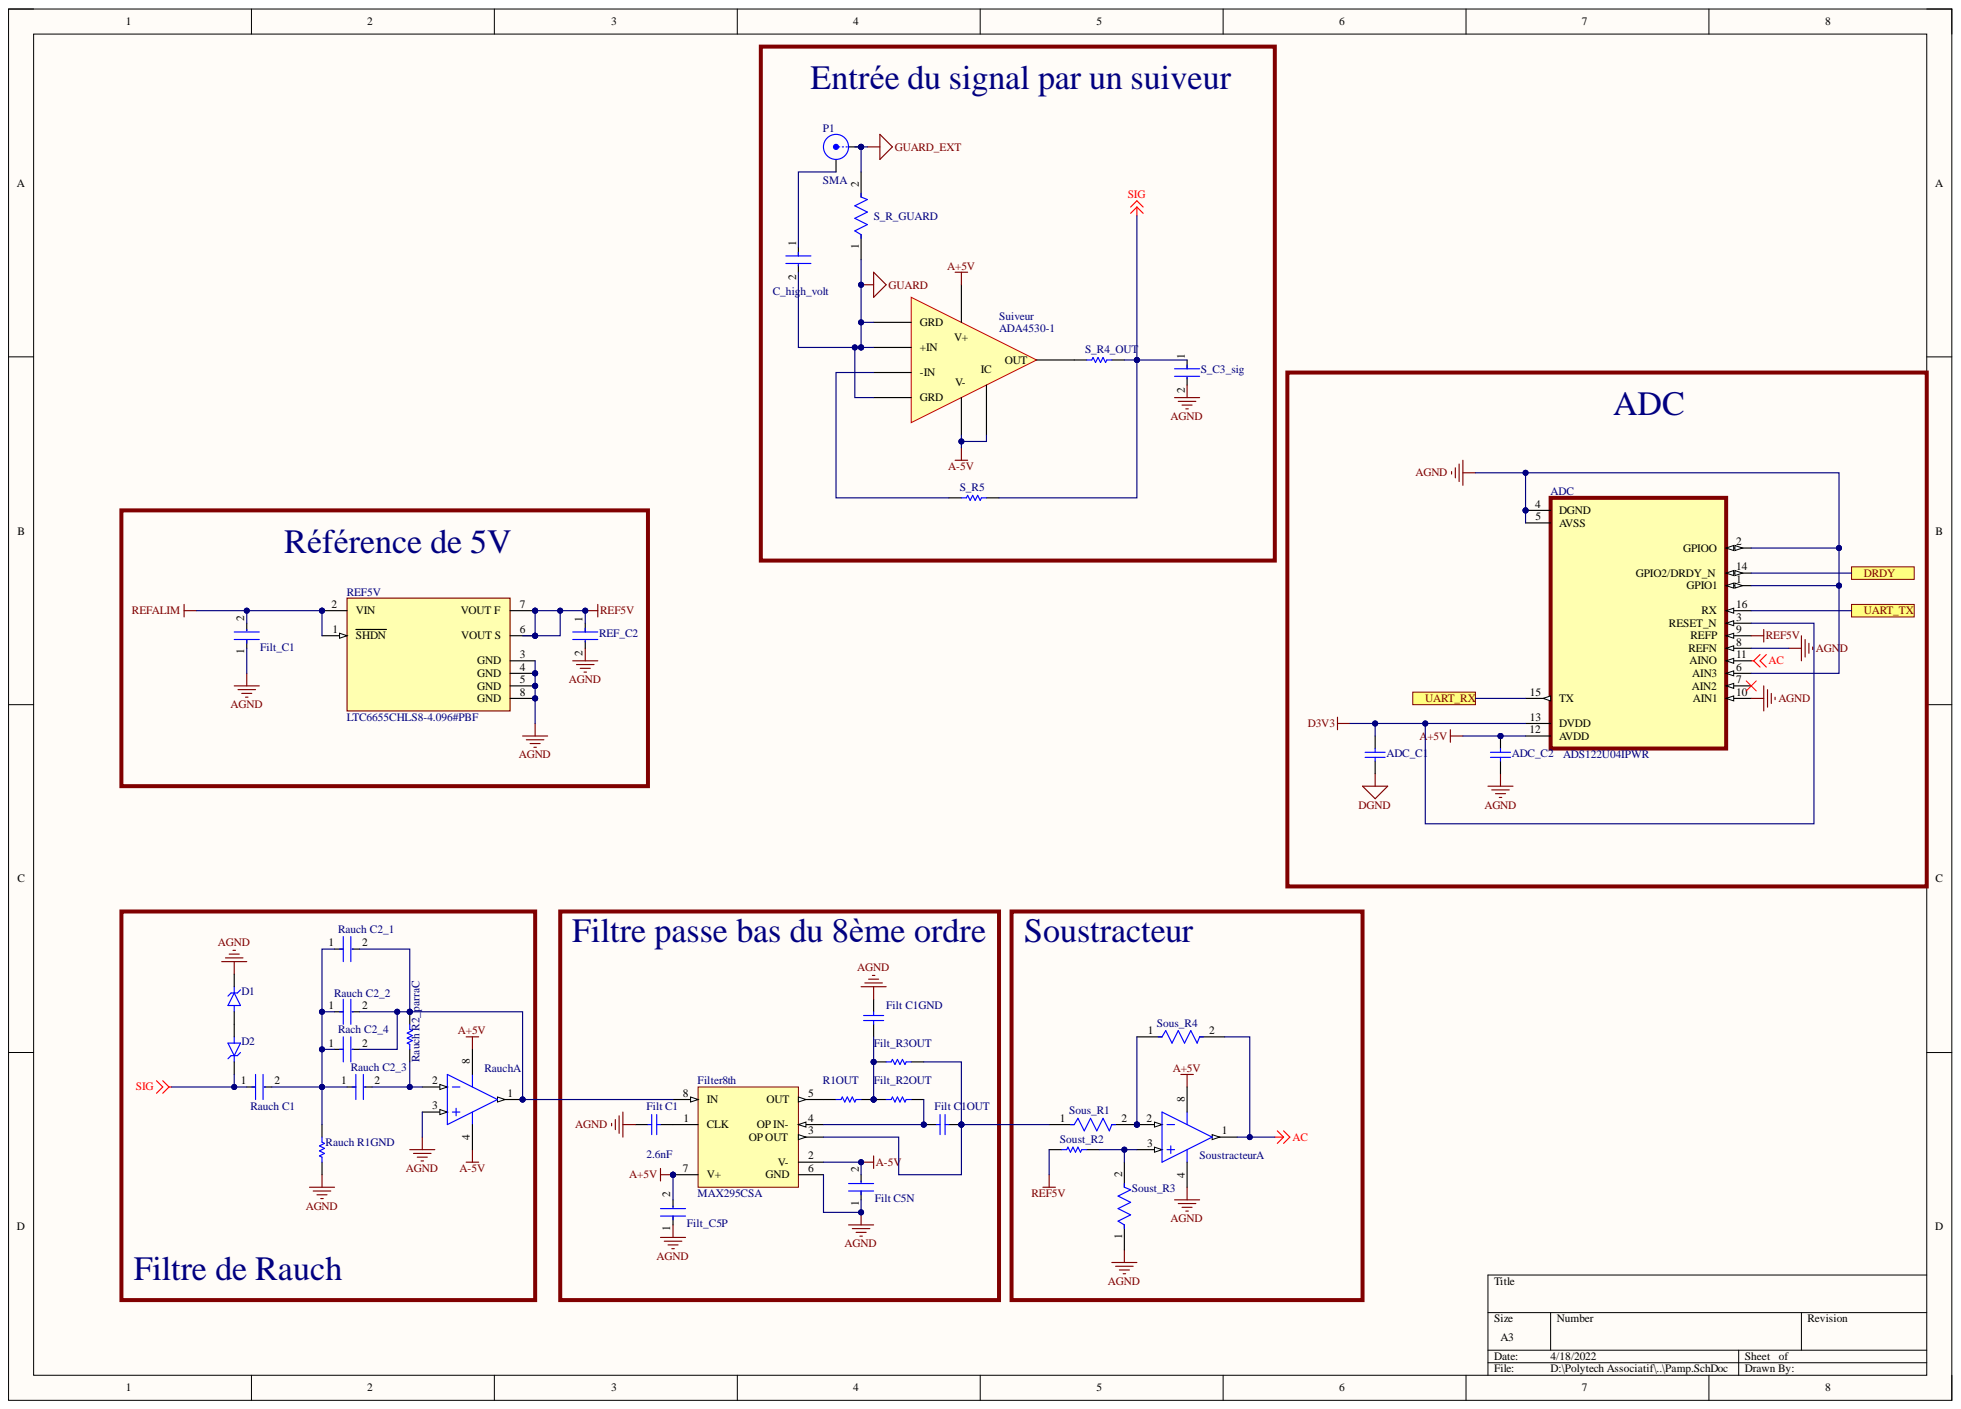
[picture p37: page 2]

Entrée du signal par un suiveur

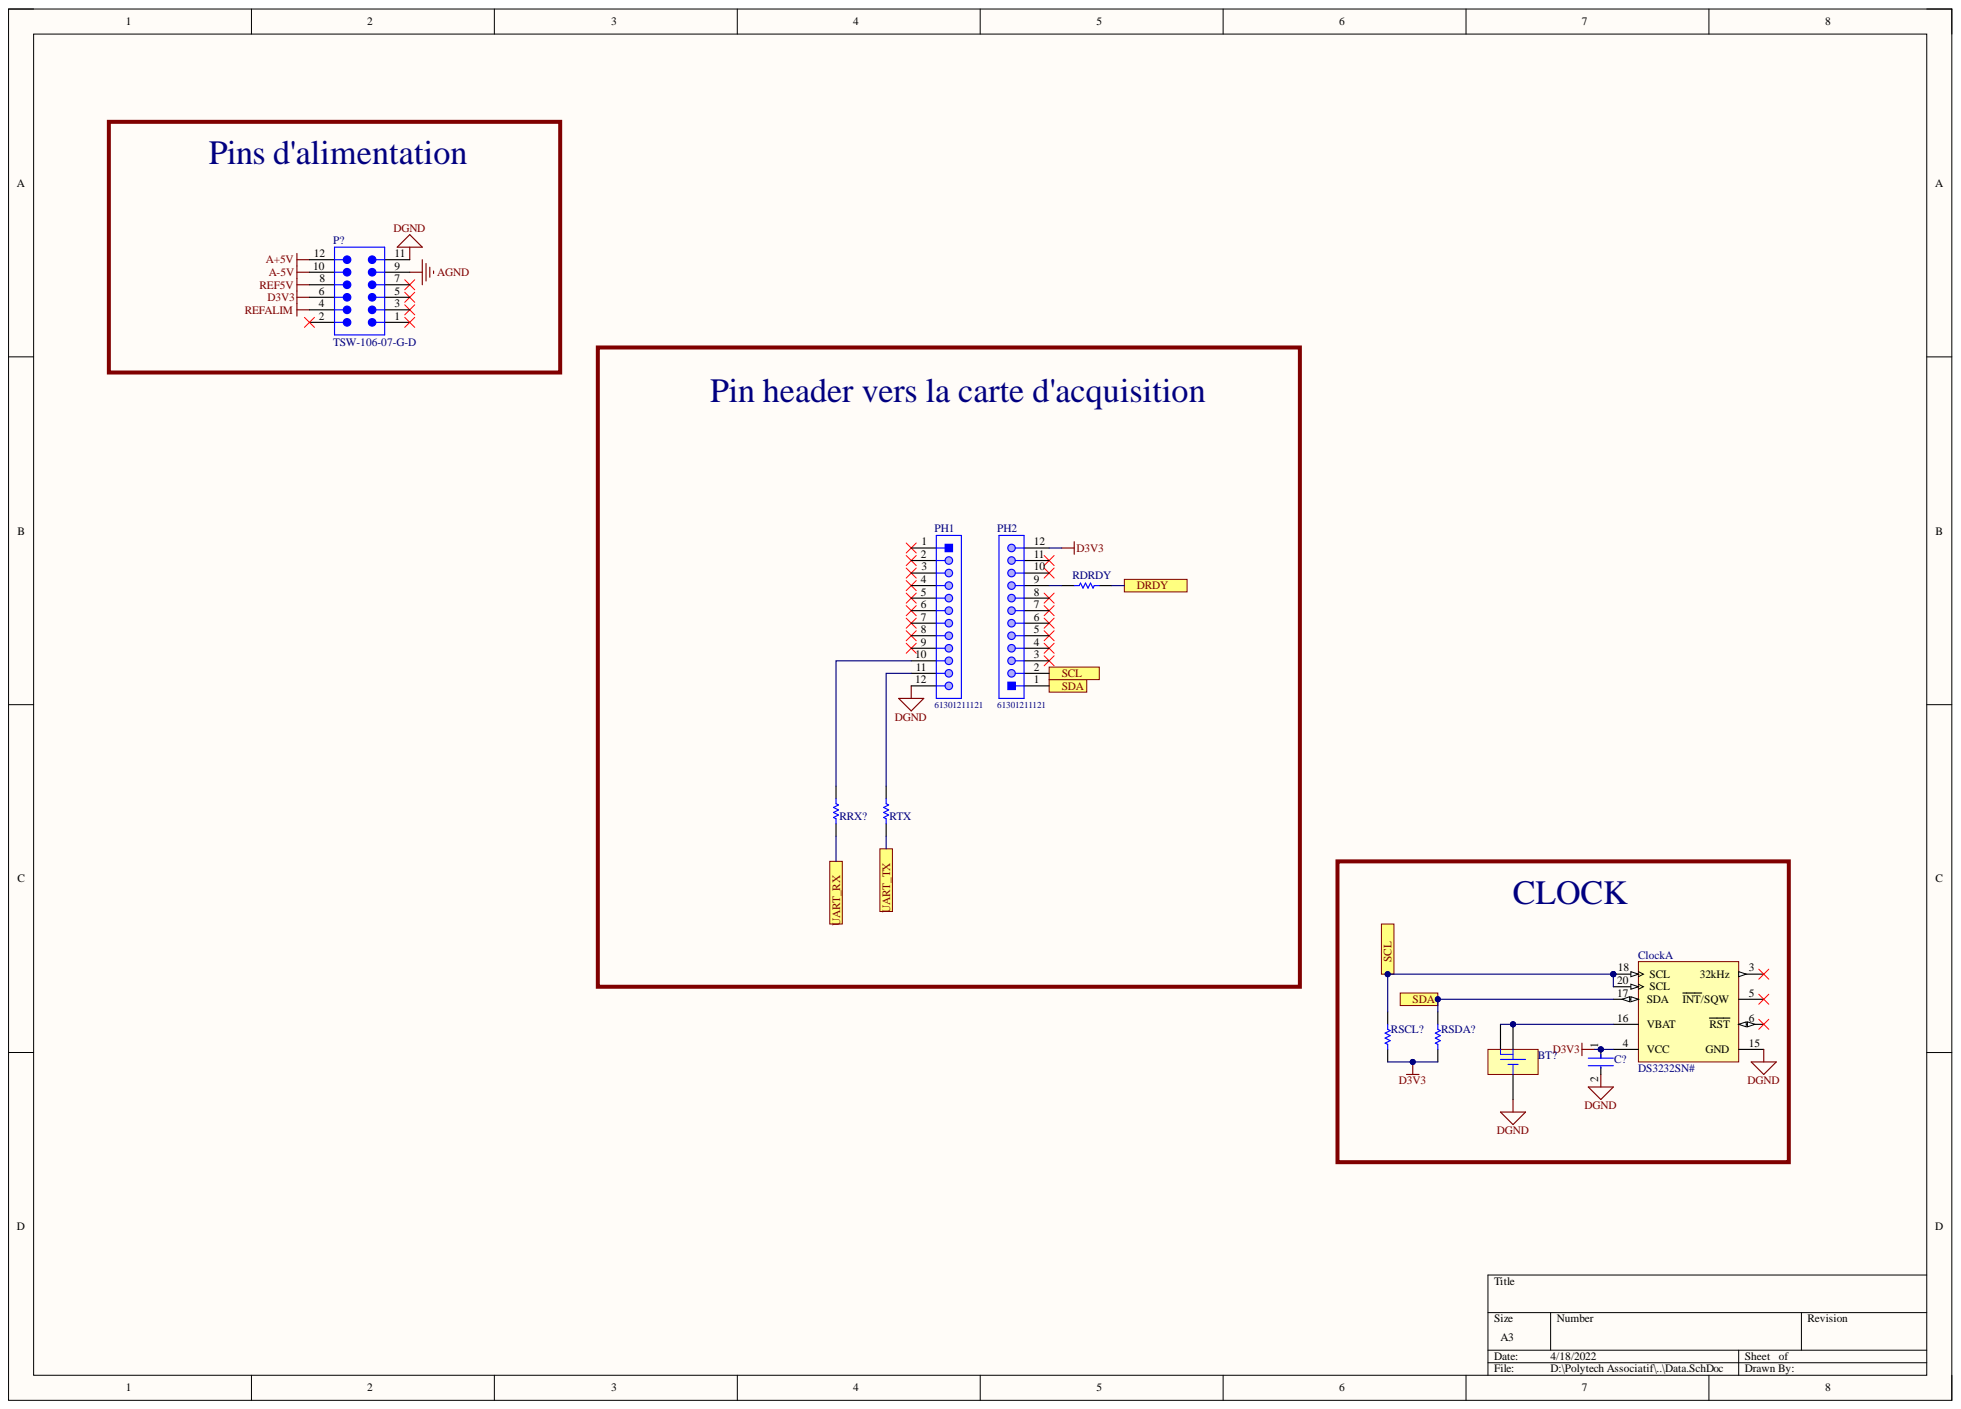
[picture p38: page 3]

10 | 9

Pin header vers la carte d'acquisition

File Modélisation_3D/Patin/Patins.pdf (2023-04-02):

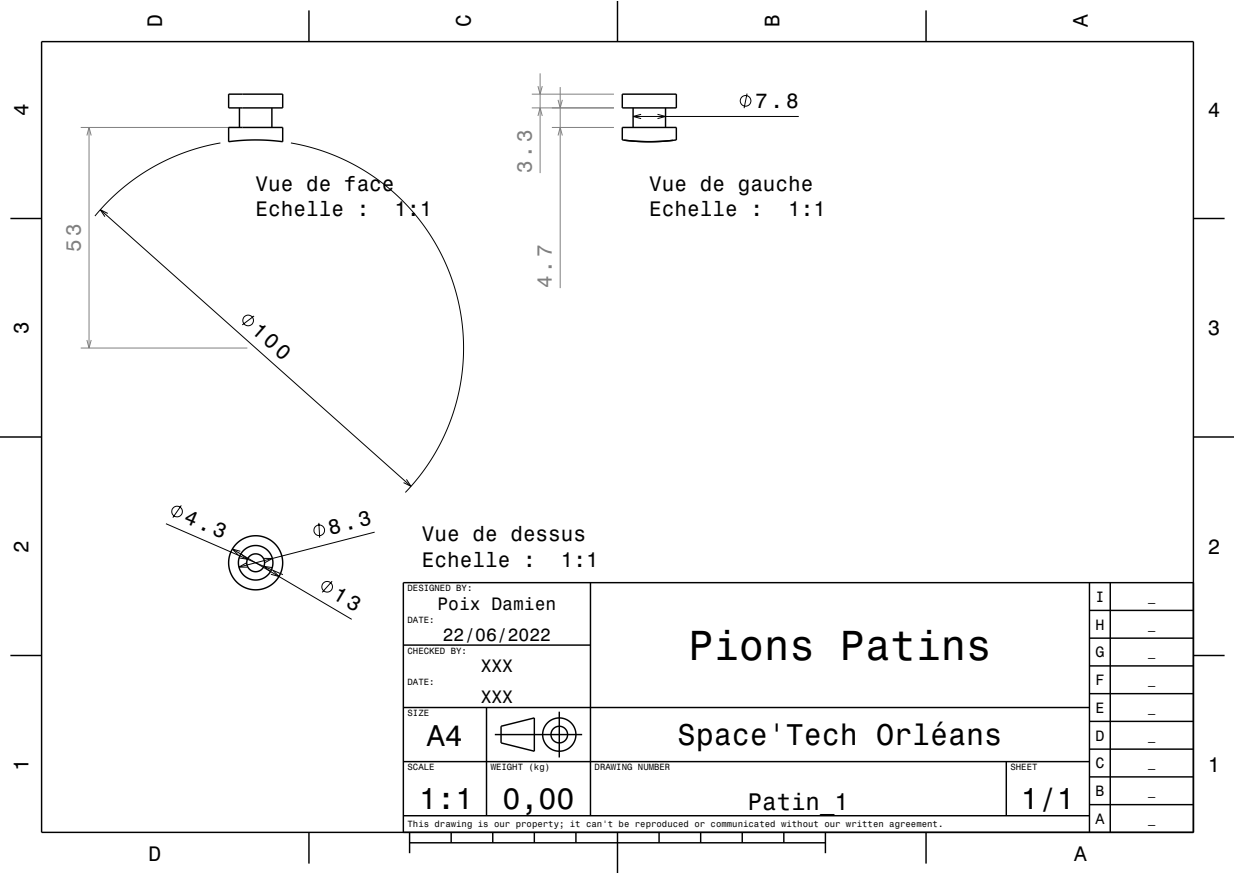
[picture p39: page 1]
CHECKED BY:

Vue de face
Echelle : 1:1

Vue de gauche

Vue de dessus

DESIGNED BY: Poix Damien DATE: 22/06/2022 | Pions Patins | I | _

SIZE A4 | | | | Space'Tech Orléans

SCALE 1:1 | WEIGHT (kg) 0,00 | DRAWING NUMBER Patin_1 | SHEET 1/1

This drawing is our property; it can't be reproduced or communicated without our written agreement.

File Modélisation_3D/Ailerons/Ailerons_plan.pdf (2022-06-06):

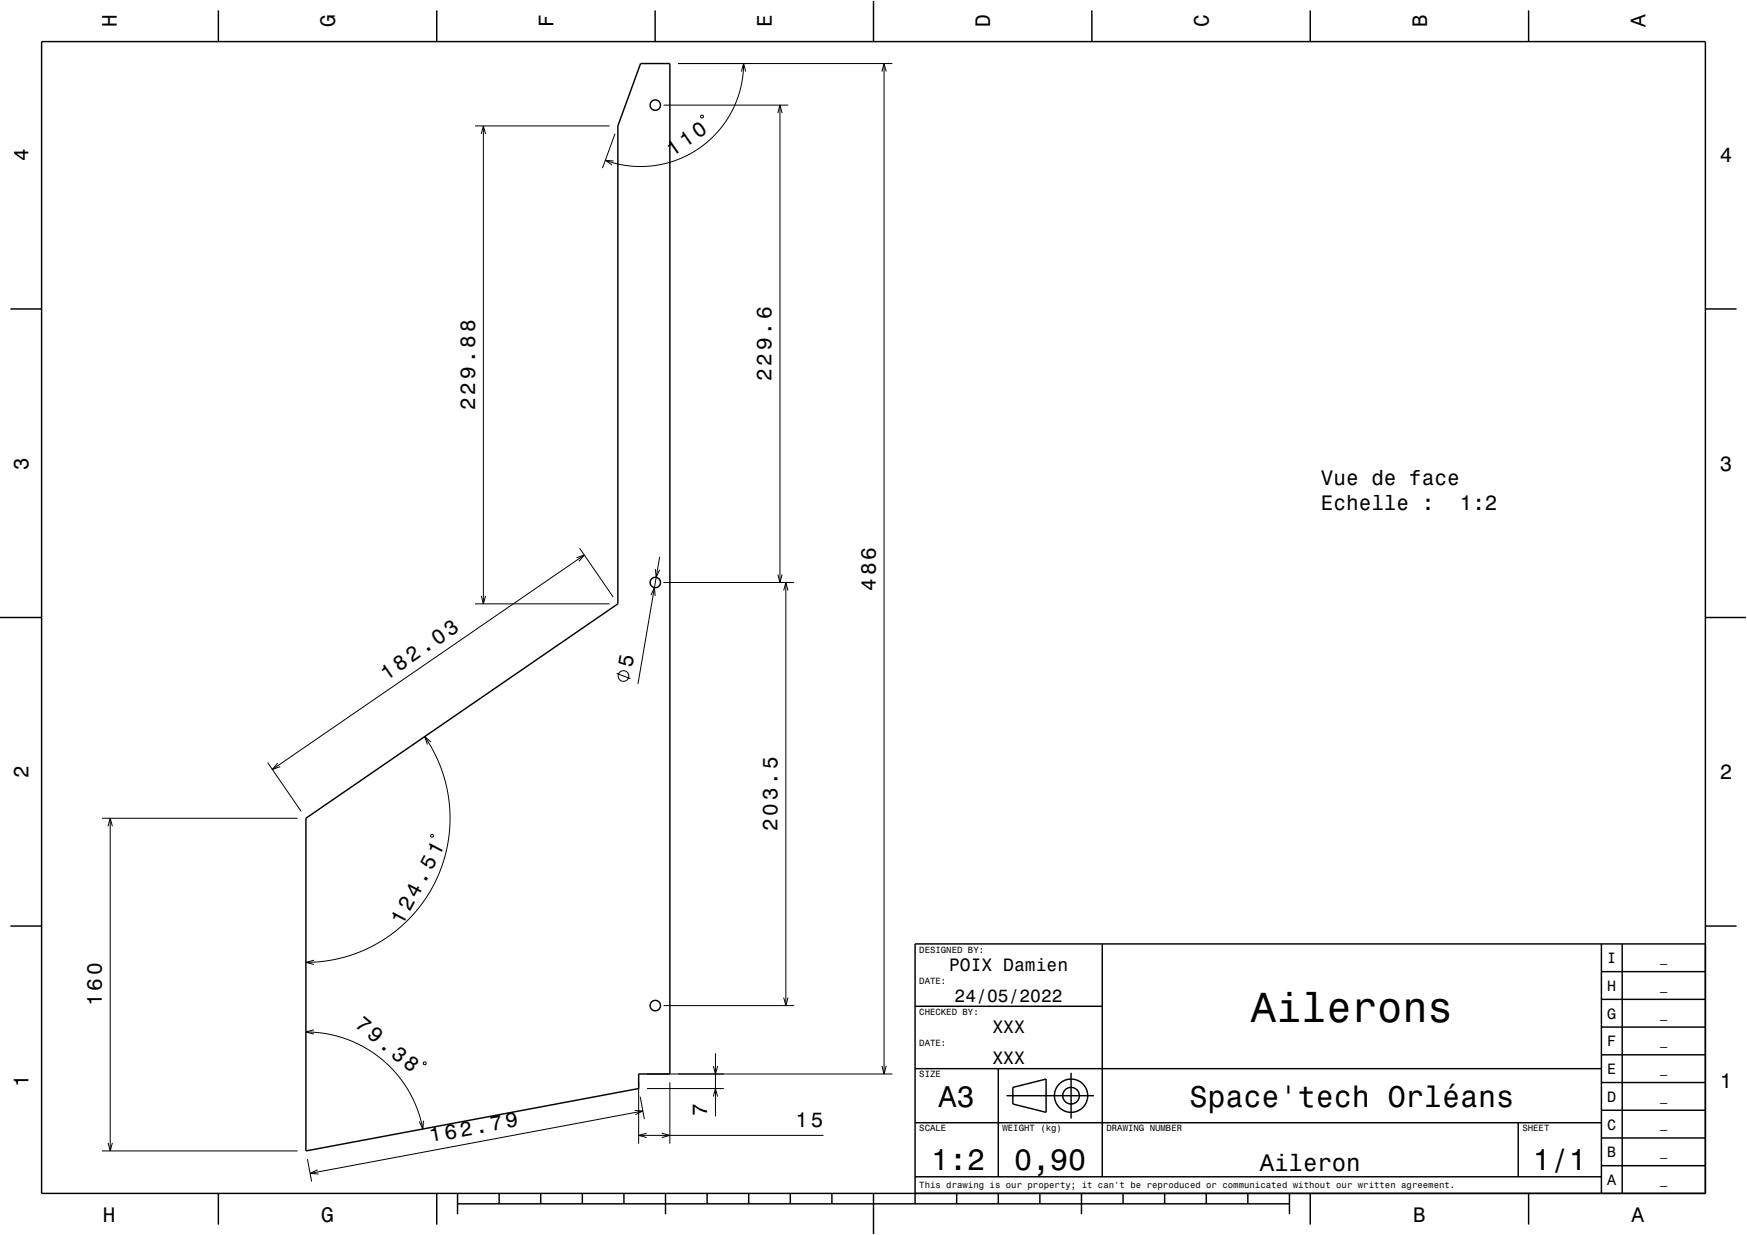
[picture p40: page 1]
CHECKED BY:

Vue de face
Echelle : 1:2

DESIGNED BY: POIX Damien DATE: 24/05/2022 | Ailerons | I | _

SIZE A3 | | | | Space'tech Orléans

SCALE 1:2 | WEIGHT (kg) 0,90 | DRAWING NUMBER Aileron | SHEET 1/1

This drawing is our property; it can't be reproduced or communicated without our written agreement.

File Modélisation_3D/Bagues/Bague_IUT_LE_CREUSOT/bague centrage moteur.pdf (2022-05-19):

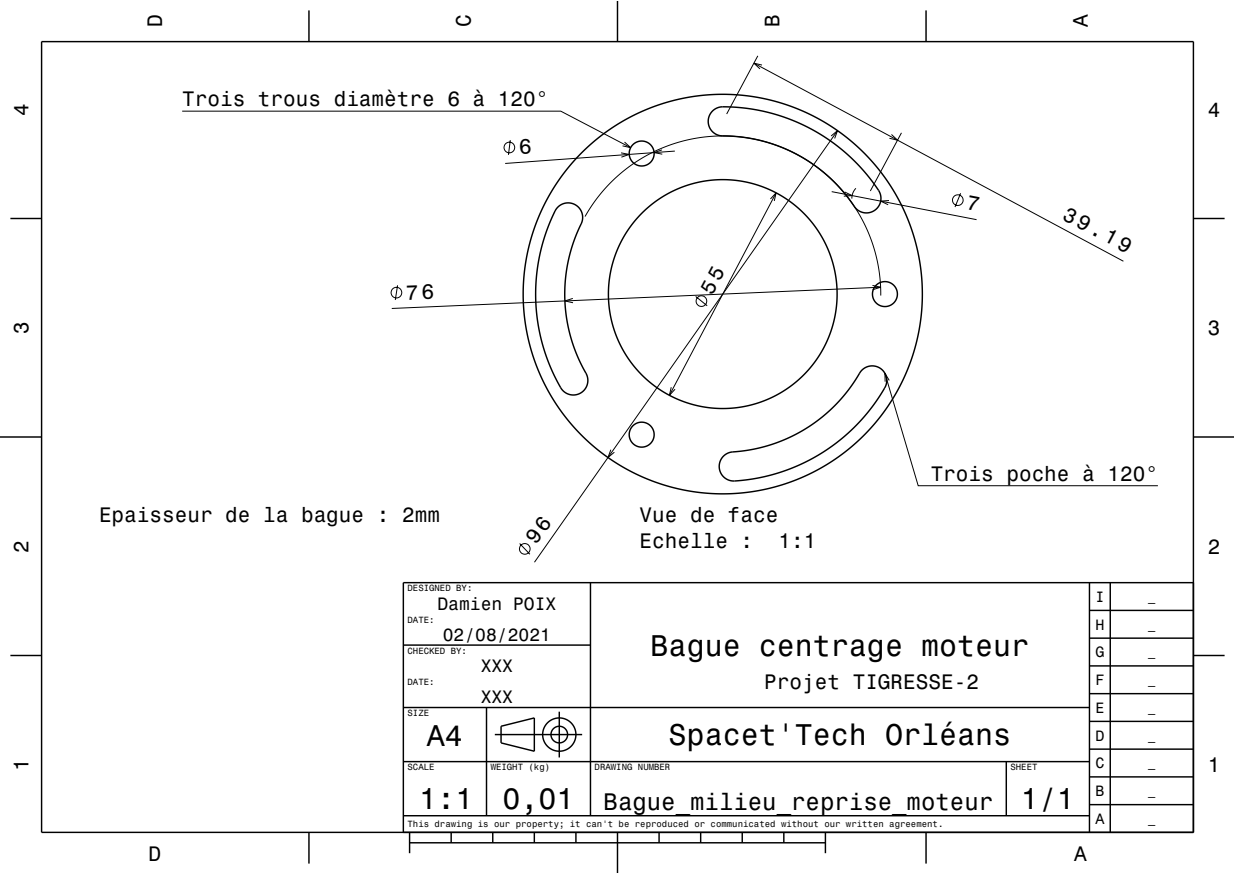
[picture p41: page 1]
CHECKED BY:; Trois poche à 120°

Trois trous diamètre 6 à 120°

Epaisseur de la bague : 2mm

Vue de face
Echelle : 1:1

DESIGNED BY: Damien POIX DATE: 02/08/2021 | Bague centrage moteur Projet TIGRESSE-2 | I | _

SIZE A4 | | | | Spacet'Tech Orléans

SCALE 1:1 | WEIGHT (kg) 0,01 | DRAWING NUMBER Bague_milieu_reprise_moteur | SHEET 1/1

This drawing is our property; it can't be reproduced or communicated without our written agreement.

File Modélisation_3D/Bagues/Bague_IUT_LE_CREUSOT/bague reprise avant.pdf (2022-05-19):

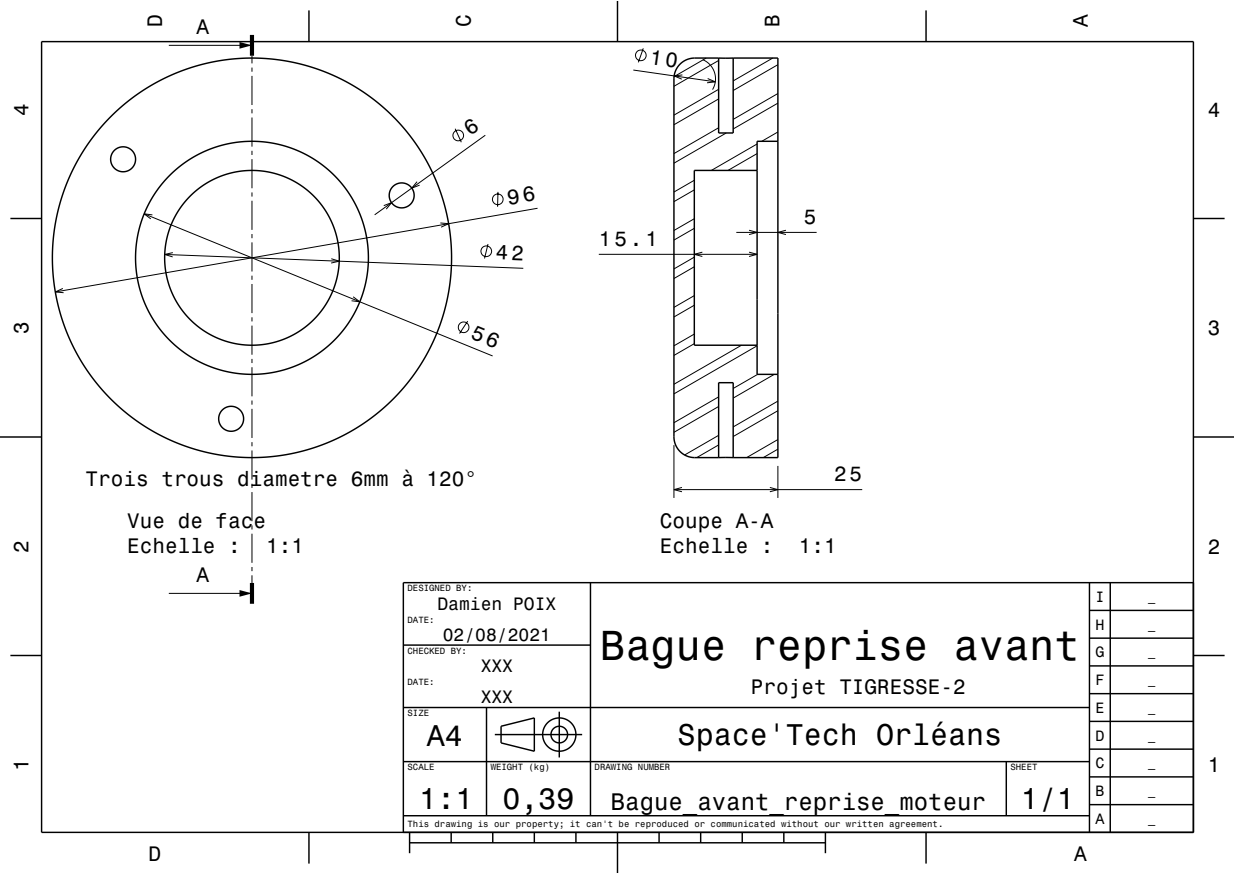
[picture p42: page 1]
CHECKED BY:; Echelle :; Coupe A-A Echelle : 1:1

Trois trous diametre 6mm à 120°
Vue de face

DESIGNED BY: Damien POIX DATE: 02/08/2021 | Bague reprise avant Projet TIGRESSE-2 | I | _

SIZE A4 | | | | Space'Tech Orléans

SCALE 1:1 | WEIGHT (kg) 0,39 | DRAWING NUMBER Bague_avant_reprise_moteur | SHEET 1/1

This drawing is our property; it can't be reproduced or communicated without our written agreement.

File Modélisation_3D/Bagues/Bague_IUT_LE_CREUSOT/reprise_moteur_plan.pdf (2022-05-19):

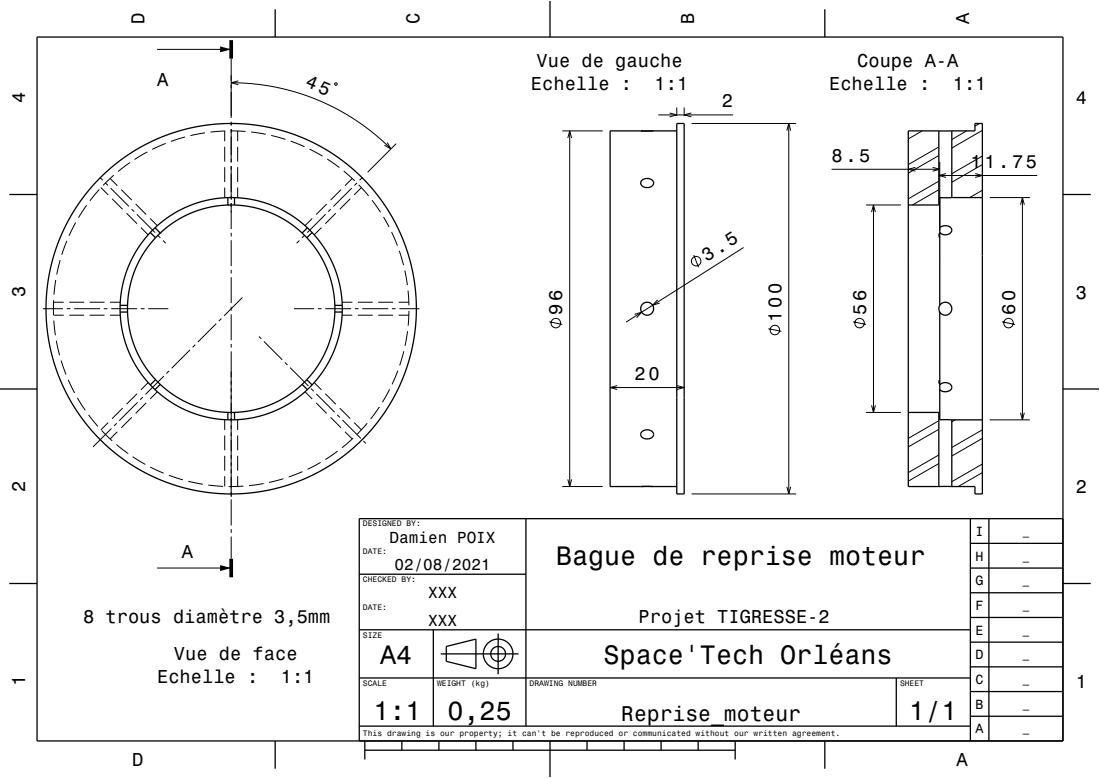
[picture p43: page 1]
CHECKED BY:; 8 trous diamètre 3,5mm; Coupe A-A Echelle : 1:1

Vue de gauche
Echelle : 1:1

DESIGNED BY: Damien POIX DATE: 02/08/2021 | Bague de reprise moteur Projet TIGRESSE-2 | I | _

SIZE A4 | | | | Space'Tech Orléans

Vue de face

SCALE 1:1 | WEIGHT (kg) 0,25 | DRAWING NUMBER Reprise_moteur | SHEET 1/1

This drawing is our property; it can't be reproduced or communicated without our written agreement.

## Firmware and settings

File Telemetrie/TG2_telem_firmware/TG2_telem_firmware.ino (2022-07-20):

#include "MPU9250.h"
#include <SPI.h>
#include <SD.h>
#include <Wire.h>
#include <Adafruit_Sensor.h>
#include "Adafruit_BMP3XX.h"
#include "UBLOX.hpp"

//global pinout
#define INT_ALTI 5
#define INT_IMU 6
#define RF_TX 9
#define RF_EN 10
#define TRG 11
#define ALARM_LED 12
#define BUZZER_PIN 13
bool serial = true;
bool logSD = true;
bool liftoff = false;

//IMU parameters
MPU9250 mpu;
float mpuQuaternion[3];
float quaternionScalar;
float mpuAccel[3];
float mpuMag[3];
float worldAccel[3];
float worldSpeed[3] = {0,0,0};
float worldPos[3] = {0,0,0};
unsigned long last_millis;

//BMP parameters
Adafruit_BMP3XX bmp;
float initialPressure = 0;
float altitude = 0;
float temperature = 0;

//SD card parameters
File root;
String rootFilename = "/logs/";
String logBuffer;

//UBLOX MAX8
UBLOX gps;

//RF
int bitrate = 2400;
int rf_delay = 0;
int rf_index = 0;
String rf_trame = "";

void setup() {
  if(serial){
    Serial.begin(115200);
    Serial.println("Start telem...");
  }
  
  initPins();
  ringtone();
  
  initMPU();
  ackTone();
  initBMP();
  ackTone();
  gps.begin(9600);
  ackTone();

  
  if(logSD){
    init_SD();
    ackTone();
  }

  //on enable la RF
  digitalWrite(RF_EN, LOW);
  
  last_millis = millis();
}

void loop() {
  if (mpu.update()) {

    mpuQuaternion[0] = mpu.getQuaternionX();
    mpuQuaternion[1] = mpu.getQuaternionY();
    mpuQuaternion[2] = mpu.getQuaternionZ();
    quaternionScalar = mpu.getQuaternionW();

    mpuAccel[0] = -mpu.getAccX();
    mpuAccel[1] = mpu.getAccY();
    mpuAccel[2] = mpu.getAccZ();

    mpuMag[0] = mpu.getMagX();
    mpuMag[1] = mpu.getMagY();
    mpuMag[2] = mpu.getMagZ();

    float dot1 = 2.0f*dot(mpuQuaternion, mpuAccel);
    float dot2 = (quaternionScalar*quaternionScalar) - dot(mpuQuaternion,mpuQuaternion);
    float cross1[3] = {0,0,0};
    cross(mpuQuaternion, mpuAccel, cross1);

    worldAccel[0] = dot1*mpuQuaternion[0] + dot2*mpuAccel[0] + 2.0f*quaternionScalar*cross1[0];
    worldAccel[1] = dot1*mpuQuaternion[1] + dot2*mpuAccel[1] + 2.0f*quaternionScalar*cross1[1];
    worldAccel[2] = dot1*mpuQuaternion[2] + dot2*mpuAccel[2] + 2.0f*quaternionScalar*cross1[2];

    //removing gravitationnal part
    worldAccel[2] -= 1; //ca a l air d etre en g askip mais c est chelou

    int dt = millis() - last_millis;
    last_millis = millis();

    //worldSpeed[0] += worldAccel[0]*9.81f*dt/1000.0f; //convertis en m/s
    //worldSpeed[1] += worldAccel[1]*9.81f*dt/1000.0f; //convertis en m/s
    worldSpeed[2] += worldAccel[2]*9.81f*dt/1000.0f; //convertis en m/s

    //worldPos[0] += worldSpeed[0]*dt/1000.0f; //convertis en m
    //worldPos[1] += worldSpeed[1]*dt/1000.0f; //convertis en m
    //worldPos[2] += worldSpeed[2]*dt/1000.0f; //convertis en m

    if(!liftoff){
      worldSpeed[2] = 0; //tant que pas decolle, egal a zero
    }

    if(millis() > 30000){//simule le liftoff vu que le trigger est pas envoye
      liftoff = true;
    }

    //traitement de l'altimetre : 
    if(bmp.performReading()){
      if(!liftoff){
        initialPressure = (initialPressure + bmp.pressure)/2;
      }else{
        altitude =  bmp.readAltitude(initialPressure/100.0f);
      }
      temperature = bmp.temperature;
    }

    gps.read();

    digitalWrite(ALARM_LED, digitalRead(TRG));

    //envoie de la RF
    if(rf_index > rf_trame.length()){
      float accMean = sqrt((worldAccel[0]*worldAccel[0])+(worldAccel[1]*worldAccel[1])+(worldAccel[2]*worldAccel[2]));
      //float agg = mpu.getPitch() > mpu.getRoll() ? :
      rf_trame = "";
      rf_index = 0;
      rf_trame +=  "$TRG:" + gps.getLat() + ";" + gps.getLon() + ";" + String(altitude,2) + ";" + String(temperature,1) + ";" + String(accMean,2) + "\n";
      //Serial.print(rf_trame);
    }else{
      writeChar(rf_trame.charAt(rf_index));
    }
    rf_index ++;
    
  
    if(logSD){ // date;time; millis; Qw;Qx;Qy;Qz; Ax;Ay;Az; Mx;My;Mz; altiBMP; temperature; lat;long
      logBuffer += gps.getDate() + ";" + gps.getTime() + ";";
      logBuffer += String(millis()) + ";";
      logBuffer += String(quaternionScalar,5) + ";" + String(mpuQuaternion[0],5) + ";" + String(mpuQuaternion[1],5) + ";" + String(mpuQuaternion[2],5) + ";";
      logBuffer += String(-mpuAccel[0],5) + ";" + String(mpuAccel[1],5) + ";" + String(mpuAccel[2],5) + ";";
      logBuffer += String(mpuMag[0],5) + ";" + String(mpuMag[1],5) + ";" + String(mpuMag[2],5) + ";";
      logBuffer += String(altitude,5) + ";";
      logBuffer += String(temperature,5) + ";";
      logBuffer += gps.getLat() + ";" + gps.getLon() + "\n"; //GPS
      saveToSD();
    }
    
  }
}

void ringtone(){
  tone(BUZZER_PIN, 659, 104);
  delay(104);
  delay(24);
  tone(BUZZER_PIN, 554, 82);
  delay(82);
  delay(47);
  tone(BUZZER_PIN, 554, 370);
  delay(370);
  tone(BUZZER_PIN, 494, 93);
  delay(93);
  delay(23);
  tone(BUZZER_PIN, 554, 117);
  delay(117);
  tone(BUZZER_PIN, 659, 267);
  delay(267);
}

void errorTone(){
  tone(BUZZER_PIN, 7500, 100);
  delay(100);
  delay(50);
  tone(BUZZER_PIN, 7500, 100);
  delay(100);
  delay(50);
  tone(BUZZER_PIN, 7500, 100);
  delay(100);
  delay(50);
}

void ackTone(){
  tone(BUZZER_PIN, 6000, 100);
  delay(100);
  delay(100);
  tone(BUZZER_PIN, 3000, 100);
  delay(100);
  delay(500);
}

void initPins(){
  pinMode(INT_ALTI, INPUT);
  pinMode(INT_IMU, INPUT);
  pinMode(RF_TX, OUTPUT);
  pinMode(RF_EN, OUTPUT);
  pinMode(TRG, INPUT);
  pinMode(ALARM_LED, OUTPUT);
  pinMode(BUZZER_PIN, OUTPUT);

  digitalWrite(RF_TX, LOW);
  digitalWrite(RF_EN, HIGH);
  digitalWrite(ALARM_LED, LOW);
  digitalWrite(BUZZER_PIN, LOW);
  
}

void initMPU(){
  float accX = 622.29;
  float accY = 8925.95;
  float accZ = -4652.39;
  float gyroX = 267.20;
  float gyroY = -410.56;
  float gyroZ = 1646.90;
  float magbiasX = 44.51;
  float magbiasY = 50.02;
  float magbiasZ = -294.45;
  float magscaleX = 0.99;
  float magscaleY = 1.03;
  float magscaleZ = 0.98;
  
  Wire.begin();
  delay(2000);

  MPU9250Setting setting;
  setting.accel_fs_sel = ACCEL_FS_SEL::A16G;
  setting.gyro_fs_sel = GYRO_FS_SEL::G500DPS;
  setting.mag_output_bits = MAG_OUTPUT_BITS::M16BITS;
  setting.fifo_sample_rate = FIFO_SAMPLE_RATE::SMPL_200HZ;
  setting.gyro_fchoice = 0x03;
  setting.gyro_dlpf_cfg = GYRO_DLPF_CFG::DLPF_41HZ;
  setting.accel_fchoice = 0x01;
  setting.accel_dlpf_cfg = ACCEL_DLPF_CFG::DLPF_45HZ;


  if(!mpu.setup(0x68, setting)) {  // 0x68 : niveau bas ; 0x69 : niveau haut
    fetchError(F("MPU connection failed. Please check your connection with `connection_check` example."));
  }

  mpu.setAccBias(accX, accY, accZ);
  mpu.setGyroBias(gyroX, gyroY, gyroZ);
  mpu.setMagBias(magbiasX, magbiasY, magbiasZ);
  mpu.setMagScale(magscaleX, magscaleY, magscaleZ);
  
}

void cross(float A[3], float B[3], float res[3]){
    res[0] = A[1] * B[2] - A[2] * B[1];
    res[1] = A[2] * B[0] - A[0] * B[2];
    res[2] = A[0] * B[1] - A[1] * B[0];
}

float dot(float A[3], float B[3])
{
    float res = 0;
    for (int i = 0; i < 3; i++)
        res = res + A[i] * B[i];
    return res;
}

void init_SD(){

  if (!SD.begin(4)) {
    fetchError(F("initialization of SD failed!"));
  }

  if(!SD.exists(rootFilename)){
    if(serial){
      Serial.println("No logs folder, creating one..."); 
    }
    
    if(!SD.mkdir(rootFilename)){
      fetchError(F("Cannot create logs folder !"));
    }
  }

  root = SD.open(rootFilename);

  int index = 0;

   while (true) {
    File entry =  root.openNextFile();
    if (! entry) {
      break;
    }
    entry.close();
    index ++;
  }

  root.close();

  if(serial){
    Serial.print("Creating the "); Serial.print(index); Serial.println(" logs file.");
  }
  
  rootFilename += String(index) + ".csv";
  root = SD.open(rootFilename, FILE_WRITE);
  
  if(root){
    root.println("date;time;millis;Qw;Qx;Qy;Qz;Ax;Ay;Az;Mx;My;Mz;altiBMP;temperature;lat;long");
  }else{
    fetchError("Errors while openning file : " + rootFilename);
  }

  logBuffer.reserve(1024);
}


void saveToSD(){
  //writing to SD card non blocking
  unsigned int chunkSize = root.availableForWrite();
  if (chunkSize && logBuffer.length() >= chunkSize) {
    root.write(logBuffer.c_str(), chunkSize);
    // remove written data from buffer
    logBuffer.remove(0, chunkSize);
  }
}


void initBMP(){
  if(!bmp.begin_I2C()){
    fetchError(F("Could not find a valid BMP3 sensor, check wiring!"));
  }

  // Set up oversampling and filter initialization
  bmp.setTemperatureOversampling(BMP3_NO_OVERSAMPLING); //oversamp to x1 comme indique par le construct pour utilisation drone
  bmp.setPressureOversampling(BMP3_OVERSAMPLING_8X); // same ..
  bmp.setIIRFilterCoeff(BMP3_IIR_FILTER_COEFF_1);
  bmp.setOutputDataRate(BMP3_ODR_50_HZ);


  for(int i = 0; i < 30; i++){
    if(bmp.performReading()){
        initialPressure += bmp.pressure;
    }else{
      if(serial){
        Serial.println(F("BMP failed to perform reading"));
        errorTone();
      }
    }
    delay(100);
  }
  
  if(initialPressure == 0){
    fetchError(F("Failed to initialize pressure"));
  }

  initialPressure = initialPressure/30;
  
}

void fetchError(String str){
  while(1){
    if(serial){
      Serial.println(str);
    }
    errorTone();
    delay(5000); 
  }
}

void writeChar(char carac){
  digitalWrite(RF_TX, HIGH);
  delayMicroseconds(1000000.0/bitrate);
  for(uint8_t i = 0; i < 8; i++){
    digitalWrite(RF_TX, ((carac >> i) & 1) ? LOW: HIGH);
    delayMicroseconds(1000000.0/bitrate);
  }
  digitalWrite(RF_TX, LOW);
  delayMicroseconds(2000000.0/bitrate);
}

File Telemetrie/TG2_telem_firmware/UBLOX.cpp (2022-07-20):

#include "UBLOX.hpp"

void UBLOX::begin(int baudrate){
    Serial1.begin(baudrate);
    delay(1000);
    writeTrame(airmodeTrame, 44);
}

void UBLOX::read(){
    while(Serial1.available() > 0){ //on read 
        char carac = Serial1.read();
        if(carac == '\n'){
            String cmd = serialBuffer.substring(1, 6);
            if(cmd == "GPRMC" || cmd == "GPGSV"){
               processData(serialBuffer); 
            }
            
            serialBuffer = "";
        }else if(carac != 13){
            serialBuffer += carac;
        }
    }
}

void UBLOX::writeTrame(uint8_t* trame, uint8_t length){
    for(uint8_t i = 0; i < length; i++){
        Serial1.write(trame[i]);
    }
}

void UBLOX::processData(String str){
    String splited[30];
    uint16_t last_index = 0;
    uint8_t index_array = 0;
    for(uint16_t i = 0; i < str.length(); i++){
        if(str.charAt(i) == ','){
            splited[index_array] = str.substring(last_index+1, i);
            index_array ++;
            last_index = i;
        }
    }
    splited[index_array] = str.substring(last_index+1, str.length());

    /*
    Serial.print("reading stupid splited values from : ");
    Serial.println(serialBuffer);
    for(int i = 0; i < index_array+1; i++){
        Serial.println(splited[i]);
    }
    */

    if(splited[0] == "GPRMC"){ //Recommended minimum data

        //time convertion
        if(splited[1] != ""){
            time = splited[1].substring(0,2) + ":" + splited[1].substring(2, 4) + ":" + splited[1].substring(4, 9);
        }else{
            time = "N/A";
        }
        
        //fix status convertion
        if(splited[2] == "A"){
            fixed = true;
        }else{
            fixed = false;
        }

        //latitude convertion
        if(splited[3] != ""){
            lat = splited[3].substring(0,2).toFloat();
            lat += splited[3].substring(2,10).toFloat()/60;
        }

        //latitude indicator
        if(splited[4] != ""){
            lat_indicator = splited[4].charAt(0);
        }

        //longitude convertion
        if(splited[5] != ""){
            lon = splited[5].substring(0,3).toFloat();
            lon += splited[5].substring(3,11).toFloat()/60;
        }

        //longitude indicator
        if(splited[6] != ""){
            lon_indicator = splited[6].charAt(0);
        }

        //data convertion
        if(splited[9] != ""){
            date = splited[9].substring(0, 2) + "/" + splited[9].substring(2, 4) + "/20" + splited[9].substring(4,6);
        }


    }else if(splited[0] == "GPGSV"){  //GNSS satellites in view
        //process in view data
        inView = splited[3].toInt();
    }else{
    //default

    }
}


String UBLOX::toString(){
    String buff = "";
    buff += date;
    buff += " ";
    buff += time;
    if(fixed){
        buff += " fixed ";
        buff += "(";
        buff += inView;
        buff += "/12) ";
        buff += String(lat,7);
        buff += lat_indicator;
        buff += " ";
        buff += String(lon,7);
        buff += lon_indicator;
    }else{
        buff += " unfixed ";
        buff += "(";
        buff += inView;
        buff += "/12) ";
    }

    return buff;
}

String UBLOX::getTime(){
  return time;
}

String UBLOX::getDate(){
  return date;
}

String UBLOX::getLat(){
  return String(lat,7);
}

String UBLOX::getLon(){
  return String(lon,7);
}

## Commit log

2022-05-11 creation de la doc sur la telem
2022-05-16 ajout MPU9250
    [componentsList.xlsx]
2022-05-18 maj compo
    [componentsList.xlsx]
2022-05-19 Ajout de docs
    [Aileron.CATPart, Antenne_boule1.CATPart, Antenne_boule2.CATPart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]
2022-05-19 maj antenne
    [componentsList.xlsx]
2022-06-06 CAD update
    [Aileron.CATPart, Aileron.stl, Antenne_boule1.CATPart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]
2022-06-06 last update compo
    [componentsList.xlsx]
2022-06-08 maj nose cone & img shema
    [noseCone.dxf]
2022-06-12 Maj CAD
    [1.2.CATPart, 1.CATPart, 1_1.CATPart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]
2022-07-07 update 07/07/2022
    [NoseConePower v19.stl, NoseConePower v21.stl, RF_holder v3.stl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]
2022-07-12 ajout interface exemple
    [NoseConePower Bottom.stl, NoseConePower Top.stl, assemblage_PCB v21.step]
2022-07-20 save pre lancement
    [0GPS.csv]
